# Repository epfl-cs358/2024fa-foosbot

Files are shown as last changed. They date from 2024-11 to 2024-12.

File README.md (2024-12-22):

# Foosbot

### Authors
- [Arthur Taieb](https://github.com/ArthurTota)
- [Ella Neike](https://github.com/Ella1807)
- [Tizian Kurz](https://github.com/TizianKurz)
- [Robin Nicole](https://github.com/Crowerade)
- [Nur Ertug](https://github.com/NurErtugn)

<details>
  <summary>Table of Contents</summary>
  <ol>
    <li>
      <a href="#project-overview">Project Overview</a>
      <ul>
        <li><a href="#built-with">Built With</a></li>
        <li><a href="#motivation">Motivation</a></li>
        <li><a href="#project-structure">Project Structure</a></li>
        <li><a href="#final-result">Final Result</a></li>
      </ul>
    </li>
    <li>
      <a href="#before-starting">Before Starting</a>
      <ul>
        <li><a href="#list-of-materials">List Of Materials</a></li>
        <li><a href="#requirements">Requirements</a></li>
      </ul>
    </li>
    <li>
      <a href="#doing-it-yourself">Doing It Yourself</a>
      <ul>
        <li><a href="#general-overview-of-tasks">General Overview Of Tasks</a></li>
        <li><a href="#lasercutting">LaserCutting</a></li>
        <li><a href="#3d-printing">3D Printing</a></li>
        <li><a href="#assembling-the-table">Assembling The Table</a></li>
      </ul>
    </li>
    <li>
      <a href="#wiring-of-the-motors">Wiring Of The Motors</a>
      <ul>
        <li><a href="#electronics-chart">Electronics Chart</a></li>
        <li><a href="#motor-and-endstop-sensor-labelling">Motor And EndStop Sensor Labelling</a></li>
        <li><a href="#protecting-motors-and-laptop">Protecting Motors And Laptop</a></li>
      </ul>
    </li>
    <li>
      <a href="#uploading-arduino-code">Uploading Arduino Code</a>
      <ul>
        <li><a href="#dependencies">Dependencies</a></li>
        <li><a href="#uploading-code">Uploading Code</a></li>
        <li><a href="#troubleshooting-arduino">Troubleshooting Arduino</a></li>
      </ul>
    </li>
    <li>
      <a href="#camera-vision">Camera Vision</a>
      <ul>
        <li><a href="#qr-code-markers">QR Code Markers</a></li>
        <li><a href="#code">Code</a></li>
        <li><a href="#installing-dependencies">Installing dependencies </a></li>
        <li><a href="#starting-camera-vision">Starting Camera Vision</a></li>
        <li><a href="#output">Output</a></li>
        <li><a href="#troubleshooting-camera-vision">Troubleshooting Camera Vision</a></li>
      </ul>
    </li>
  </ol>
</details>

## Project Overview

### Built With
* [][Python-url]
* [][Cpp-url]

### Motivation 
Table football, commonly known as foosball or table soccer, is a fast-paced game inspired by association football. Players aim to score goals by maneuvering rods with miniature figures representing football players from two opposing teams. While typically enjoyed by 2-4 players, traditional foosball is not designed for solo play.

This project seeks to develop a foosball table playable by a single player using an Arduino Uno microcontroller. The system will allow one side of the game to be automated and controlled via a computer program, while a human player operates the other side. The automated system will manage two axes of movement for each rod: rotation and linear displacement.

However, to simplify development and reduce costs, the prototype will use a smaller-scale foosball table with two rods per side instead of the standard four. This scaled-down design reduces system complexity and enhances motor responsiveness, making it more suitable for our project goals.

### Project Structure
- `Admin` : Contains images used in the README
- `CAD` : Contains all the CAD stl files as well as the dxf files for lasercutting
- `Hardware` : Contains the electronic circuit diagram and a document with hardware component specifications
- `Software` : Contains all the code
  - `Software/Algorithms/followBall` : Contains the Arduino code for controlling the motors and handling the game logic
  - `Software/Camera/cv/python-webcam` : Contains the python code for the computer vision as well as the QR Markers to printout

### Final Result 

https://github.com/user-attachments/assets/f8ba40bc-5658-4df2-8fb3-47cc1d8da43e

Table

Circuitry

<p align="right">(<a href="#readme-top">back to top</a>)</p>

## Before Starting

### List of Materials 
You will need to buy:
- [x] 4 17HS4401 Stepper Motors
- [x] 4 A4988 Motor Drivers
- [x] 4 End stop Sensors
- [x] 1 Arduino Uno
- [x] 1 USB cable to connect to the Arduino
- [x] 1 CNC Shield
- [x] 1 USB Isolator
- [x] 1 Logitech Webcam C270
- [x] 2 Aluminium Profile _20_ _x_ _20mm_ of length _410mm_
- [x] 1 12V Power Supply
- [x] 1 Power Supply Plug
- [x] 2 _~1_ _meter_ GT2 _6mm_ belt
- [x] 1 _1_ _meter_ WS2813 LED Strips
- [x] 1 Bread board
- [x] 2 Metal Bars with diameter _15_ _mm_ length _1200__mm_
- [x] 2 Metal Bars with diameter _8_ _mm_ length _1200__mm_
- [x] 4 Ball Bearings that allow for both rotational and linear motion
- [x] 8 Wheels (Something like [this](https://www.zyltech.com/zyltech-20-series-wheel-pulley-bearing-for-2020-aluminum-extrusion-v-slot-compatible/))
- [x] 2 Pully
- [x] Jumper cables
- [x] 1 ball

To assemble you also need the following

Pole Components:
- [x] 48 _M3_ screws with nuts, length _8mm_
- [x] 12 _M2.5_ screws with nuts, length _12mm_
- [x] 2 _M4_ screws with nuts, length _16mm_

Mechanical Components:
- [x] 14 _M3_ screws with nuts, length _8mm_
- [x] 2 _M3_ screws with nuts, length _25_mm
- [x] 16 x _M2.5_ screws with nuts, length _8mm_
- [x] 2 x steel bars, diameter _4mm_, length _3.2mm_
- [x] 2 x steel bars, diameter _4mm_, length _2.2mm_

### Requirements 
have access to:
  -	3D printer with TPU filament
  -	3D printer with PET filament
  -	Laser cutting machine
  -	PlexiGlass _10mm_
  -	MDF board _3mm_
  -	MDF board _4mm_
  -	MDF board _5mm_
  -	MDF board _10mm_
  -	Driller
  -	Bunch of different screwdrivers
  -	Soldering kit

<p align="right">(<a href="#readme-top">back to top</a>)</p>

## Doing it yourself

### General Overview of tasks
- Lasercut
- 3D Print
- Assemble the Table
- Wire up the motors to the Arduino
- Set up the Camera Vision

### LaserCutting
Lasercut with the right MDF thickness (is in the file names): [DXF files](CAD/laser_Cuted_Components) 

### 3D Printing
3D Print the following pieces from the CAD:

For 3D printing of Pole Components: [STL files](CAD/PoleComponents) 

- 4 x Players with _15mm_ radius (Computer Controlled) -> Perimeter 6
- 4 x Players with _8mm_ radius (Human Controlled)     -> Perimeter 6
- 2 x GardianStop _15mm_ radius                        -> Perimeter 2
- 2 x GardianStop _8mm_ radius                         -> Perimeter 2
- 4 x Bumpers with _15mm_ radius                       -> Perimeter 2
- 4 x Bumpers with _8mm_ radius                        -> Perimeter 2
- 8 x Bushing with _15mm_ radius                       -> Perimeter 3
- 8 x Bushing with _8mm_ radius                        -> Perimeter 3
- 2 x Handles                                          -> Perimeter 5
- 2 x End Caps _8mm_ radius                            -> Perimeter 3
- 2 x End Caps _15mm_ radius                           -> Perimeter 3

For 3D printing of Mechanical Components: [STL files](CAD/MechanicalComponents)
  
- 2 x Standing Motor holder                            -> Perimeter 2
- 2 x Rotation Motor holder                            -> Perimeter 2
- 2 x Motor to Pole Connector                          -> Perimeter 5
- 2 x Railing holder without pulley                    -> Perimeter 2
- 2 x Railing holder with pulley                       -> Perimeter 2
- 2 x pulley                                           -> Perimeter 2
- 2 x wheels (to put at the end of the belts)          -> Perimeter 2
- 4 x Belt to motor Platform Connector                 -> Perimeter 5

Our 3D printing steps: 
Use Fusion 360 to create and edit the pieces 

Open Prusaslicer to prepare pieces for impression: 
1. Select Filament PETG
2. Select Printer MK4 with 0.4 nozzle or i3 MK3S & MK3S+
3. Select Print Setting 0.20mm QUALITY
4. Place and add necessary supports to print out pieces correctly
5. Edit the perimeter of the pieces for more resistance if needed
6. Slice and Print

For the Bumpers:
Open Prusaslicer to prepare pieces for impression: 
1. Select Filament NinjaTek NinjaFlex TPU
2. Select Printer i3 MK3S & MK3S+
3. Select Print Setting 0.20mm QUALITY
4. ! don't use supports
5. Place pieces and Slice 
6. Add glue to printing bed
7. Print 

When slicing be careful of the surface on which you print your pieces, to ideally minimize supports needed or place them in a smart way. 

### Assembling The Table 
1. Glue all the mdf pieces together with wood glue
2. Add ball bearings and screw bushings
3. Insert poles in one bushing and add the bumpers, add players with a spacing of _184mm_ between player/gardianStop, add gardianStop
4. Insert poles into second bushing and add endcaps and handles
5. Follow picture in Final Result to finish assembly

Foosbot Assembly Animation

<p align="right">(<a href="#final_result_top">back to Final Result</a>)</p>

For ball reception place the following way
BallReception

<p align="right">(<a href="#readme-top">back to top</a>)</p>

## Wiring of the Motors

### Electronics Chart
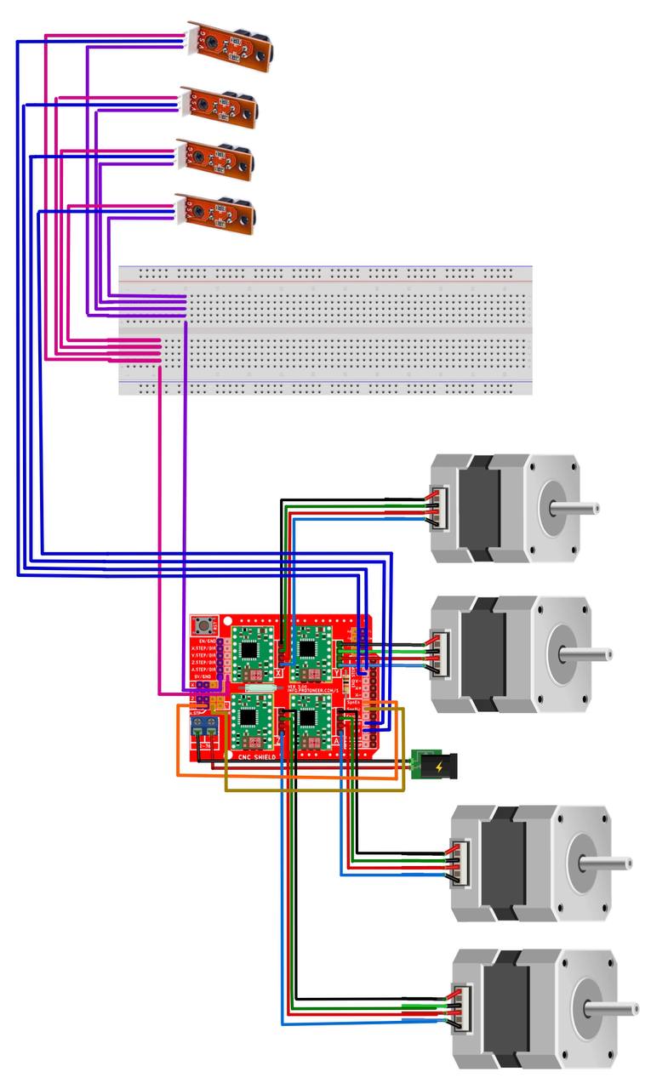
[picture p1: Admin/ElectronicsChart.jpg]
ElectronicCircuit


CNC shield mounted on top of the Arduino Uno , reset buttons should be aligned 
CNC shield-Arduino Uno pin correspondance
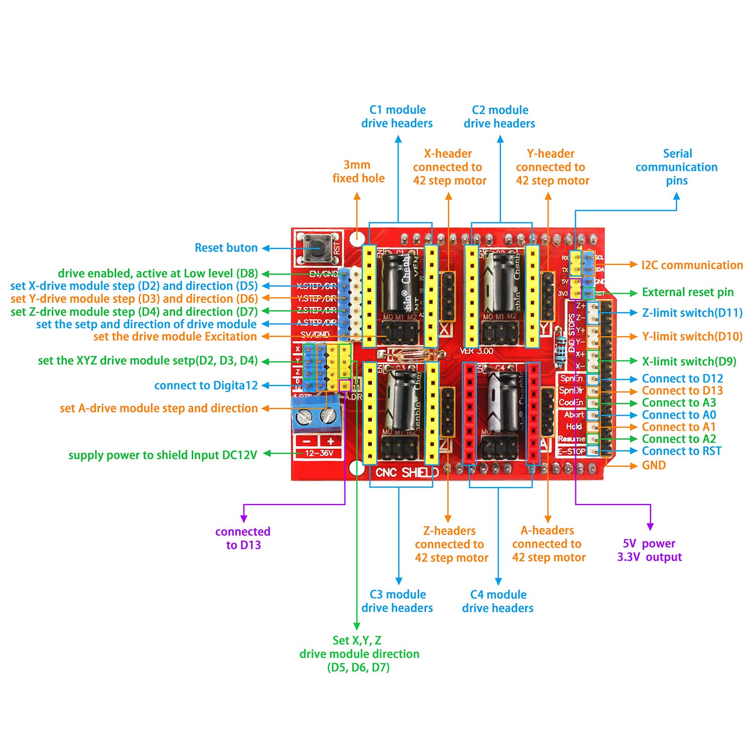
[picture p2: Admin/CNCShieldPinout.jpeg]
CNCShieldPinout


When installing the A4988 Motor Drivers set the voltage in alternate current to 1.2V
by turning the screws and using a multimeter. 

### Motor And EndStop Sensor Labelling
On the CNC Shield there are 3 slots for motor drivers labelled X, Y, Z, A. In the picture below you see to which motor they should be connected to.

The End stop sensors have three cables that need to be connected, one to the ground, one to the 5V Power and one to the correct pins on the CNC Shield. The mapping of the position of the end stop sensors to the pins on the CNC Shield are shown in green in the picture below.


### Protecting Motors and Laptop
Always connect the Arduino via a USB-Isolator to your laptop and ideally don't charge your laptop while it is connected to the Arduino.
It is also important that you unplug the power and the Arduino before changing anything on the wiring or manually moving the motors.
Generally it is also advised to disconnect the power and the arduino whenever you're not using them.
Also note that the motor drivers on the CNC shield might head up a bit if used for a long period of time.

<p align="right">(<a href="#readme-top">back to top</a>)</p>

## Uploading Arduino Code

### Dependencies
You need to have [Arduino IDE](https://www.arduino.cc/en/software) installed, as well as the libraries

### Uploading Code
1. Open the code for the Arduino in `/Software/Algorithms/followBall/followBall.ino`
2. Connect the Arduino via the USB Isolator to your laptop
3. Press the upload button in the top left of the Arduino IDE

### Troubleshooting Arduino

- If you get a compilation error, check whether you have all libraries installed.
- If you get an error while uploading, check whether you have selected the right board and port and try again.
- If the motors don't move check your wiring. If that doesn't help check the voltage of the motor drivers using a multimeter. Also the [documentation](https://docs.cirkitdesigner.com/component/2c4686b3-94a4-4df1-aee0-7a9f67fd5f2e/cnc-shield-v3) of the CNC shield might help.

<p align="right">(<a href="#readme-top">back to top</a>)</p>

## Camera Vision

### QR Code Markers
You need to print out the 4 QR Code Markers stored in the file
[`/Software/Camera/cv/python-webcam/ArUco markers.pdf`](https://github.com/epfl-cs358/2024fa-foosbot/blob/main/Software/Camera/cv/python-webcam/ArUco%20markers.pdf)
and cut them out. 

You then have to tape the QR Codes into the Right corners. Note that the top left corner, marked red in images below, should always point towards the corner. The QR Codes are numbered (see below) and they need to be in the right corners, according to the image below.

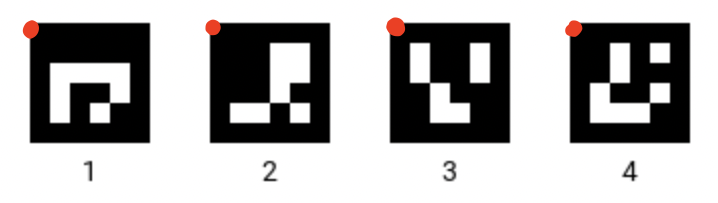
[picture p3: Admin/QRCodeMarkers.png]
QRCodeMarkers


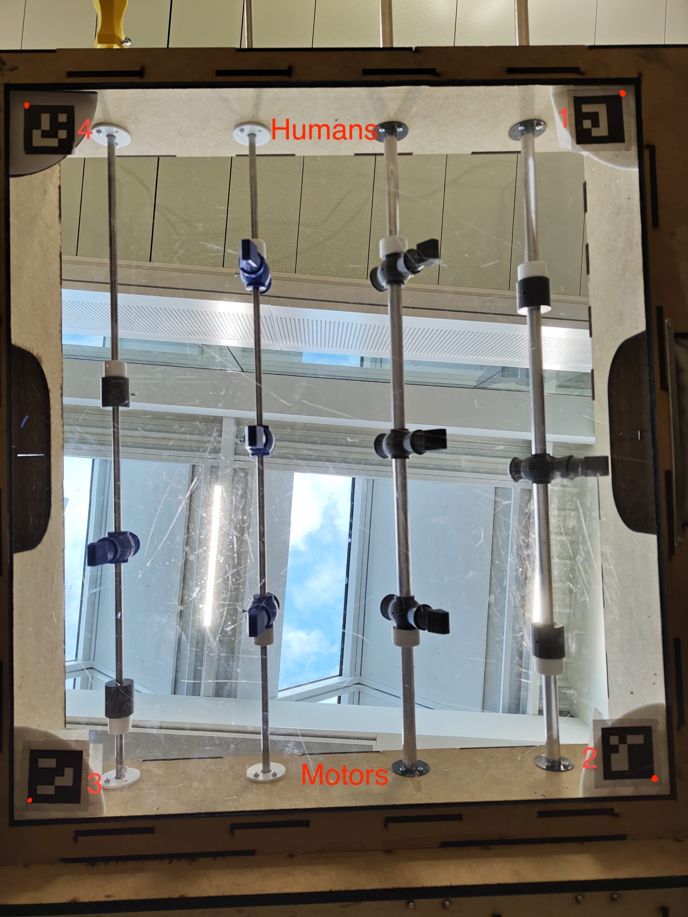
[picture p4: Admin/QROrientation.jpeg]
QROrientation


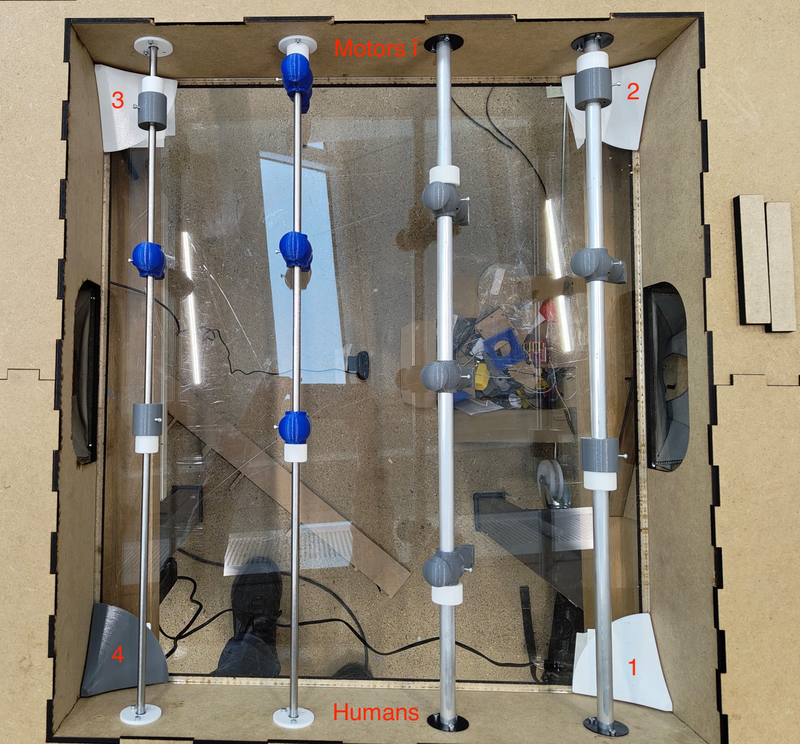
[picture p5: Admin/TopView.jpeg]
TopView


__It is important that the Codes are at in the right corners and oriented the right way!__
Otherwise the camera vision will not detect the playing field correctly and do a weird transformation or cut of some part.

### Code
The code for the Camera Vision is located in the folder
[`/Software/Camera/cv/python-webcam/main.py`](https://github.com/epfl-cs358/2024fa-foosbot/blob/main/Software/Camera/cv/python-webcam/main.py)

### Installing Dependencies
You need to have python installed on your computer (See [here](https://realpython.com/installing-python/) an article how to install python).
You als need the following libraries:
- [PySerial](https://pypi.org/project/pyserial/)
- [opencv](https://opencv.org/)

If you are on linux or macOS and have pip installed you can simply run 

```commandline
pip install pyserial
pip install opencv
```
If you're having trouble, check with your package manager whether it accepts pip installs.

### Starting Camera Vision
Note that you have to close all Serial monitors in the ArduinoIDE since it prevents the computer vision from opening the port. You can open it again when the computer vision is running.
2. Plug in the Logitech webcam,
1. Plug in the Arduino UNO,
3. Navigate to folder ` Software/Camera/cv/python-webcam `,
4. Run ` ./main.py `.

If you want to know how to use different flags, type `./main.py --help`.

### Output

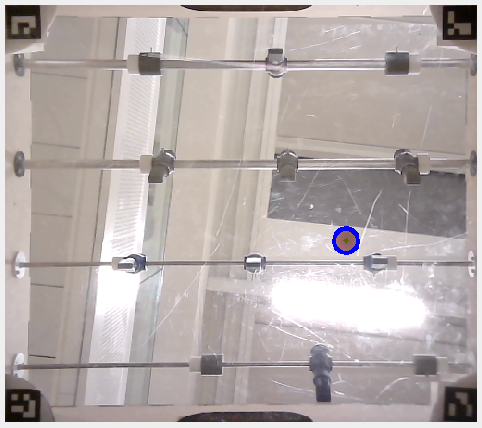
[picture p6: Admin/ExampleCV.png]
ExampleCV


By default the camera should open a window called Output which displays the area in which the ball can be detected. If  the ball is detected, there should be a blue circle around it.

### Troubleshooting Camera Vision
- If the camera is not activating properly, try changing the parameter of the call to the ` cv2.VideoCapture ` function to another number (usually 0 or 2). You can also use the `-i` flag for that.
- If the camera vision does a weird transformation then the QR Codes are not placed in the right corners.
- If the output doesn't show the entire field, then the QR Codes might not be oriented correctly (Top left corner ins't pointing towards the corner).
- If the ball isn't detected then you might need to change the allowed range for the radius (line 37 in [`main.py`](https://github.com/epfl-cs358/2024fa-foosbot/blob/main/Software/Camera/cv/python-webcam/main.py)). By default it is set to accept radius between 25 and 31. This works well for us on Macbooks but we observed that on Linux a range of 10 to 15 is appropriate.
- If the code has a problem uploading to the arduino try doing the following (sometimes the port has a problem):
1. Stop the computer vision
2. Make sure you have no serial monitor open on the arduino ide and close all other sketches
3. Plug in the arduino uno again and upload the code
4. Start the computer vision again 

Remember that you can use different flags to debug the computer vision. For example you can display views of different stages of computer vision (Marker detection, image transformation, etc.) using the --w or --windows flag or you can disable the Serial output if no Arduino is connected by  using the -n or --no-ser-out flag.

<p align="right">(<a href="#readme-top">back to top</a>)</p>

[Python.org]: https://img.shields.io/badge/Python-brightgreeen?style=flat&logo=python&logoColor=FFE873&color=306998
[Python-url]: https://www.python.org/
[Cpp.org]: https://img.shields.io/badge/C%2B%2B-blue?logo=cplusplus
[Cpp-url]: https://isocpp.org/

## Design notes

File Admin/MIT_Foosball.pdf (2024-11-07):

# Foosbot: A Single Player Table Football

CS-358: Making Intelligent Things — Team Project Proposal

Group Members:
Nur Ertug, Tizian Kurz, Arthur Taieb, Robin Nicole, Ella Neike

## Description

Table football, also known as foosball or table soccer, is a game based on association football. The objective is to move the ball into the opponent’s goal by manipulating rods with figures resembling football players of two opposing teams. This fast-paced game is typically played by 2-4 players, but it is not designed for solo play.
Our project proposes the creation of a Foosball table that can be played by a single player, with the help of an Arduino Uno board. Our vision involves a program executed from a computer connected to the microcontroller, controlling one side of the game, while a human player controls the other side. This system should at least be able to rotate the handles and displace them, considering two axes of movement per pole.
A traditional foosball table is as large as a standard table and has four handles per side. However, for the sake of our project’s budget and complexity, the prototype will be based on a smaller version with only two handles per side. This approach will reduce system complexity and improve motor reaction times.

## Game Setup

- A red button is placed on one side of the main game surface to activate the game.
- The button can be pressed during the game to stop the action and restart the game.
- Double-clicking the red button stops the game completely.
- A small digital screen shows:

– Game Instructions

– Current score while playing

1

## Game Level Selection

The single player can choose their competitor’s difficulty level: beginner, intermediate, or advanced.

## Player Specification

The player can select their team color and name via the digital screen. When the player scores, a special congratulatory message will be displayed on the screen.

## Gameplay Mechanics

Controls

The human player uses keyboard controls or mouse inputs to control the players. Instructions will be provided on how to maneuver.

Game Rules

Standard foosball rules apply.

Game Levels

- Beginner: Basic movements with error replacement in shooting skills.
- Intermediate: Better positioning, including ball passing between players on the same row.
- Advanced: Fast moves, improved tactics based on the human player’s actions.

## Visuals and Sound

- Sound: Hand clap sound effects when the single player scores.
- Visuals: Congratulatory messages displayed on the digital screen when the player scores.

## Game Flow Parametrics

- Digital Display: Displays current score.
- Red Button: Controls for resetting, starting, and stopping the game.
- Match Timer: A 30-minute counter automatically ends the game.

2

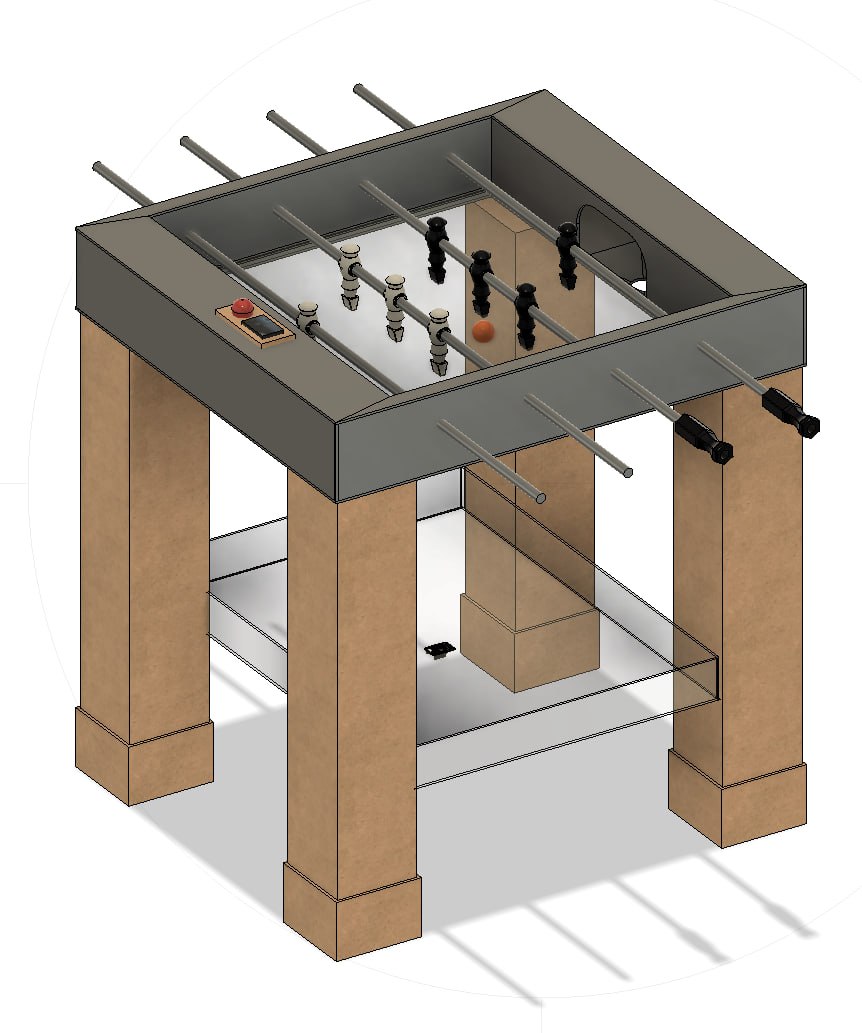
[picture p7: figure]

Figure 1: Isometric View of Foosball Table Structure

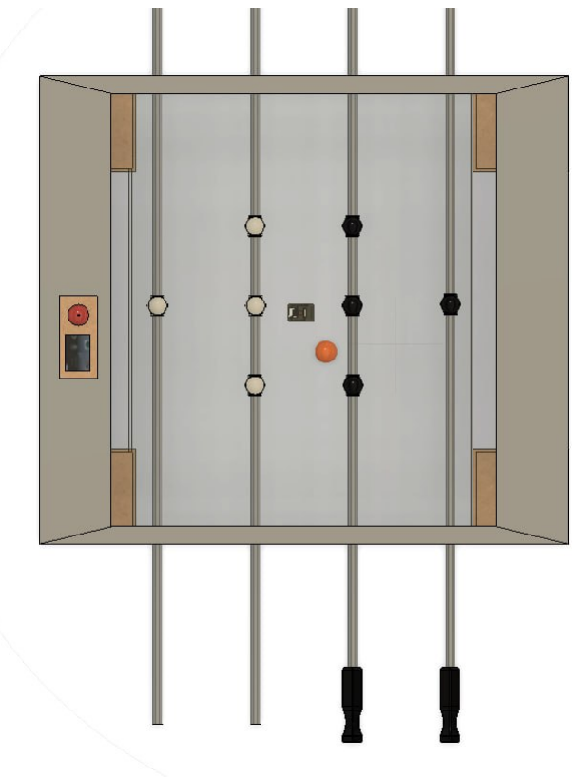
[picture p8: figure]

Figure 2: Top View of the Foosball Table Structure

3

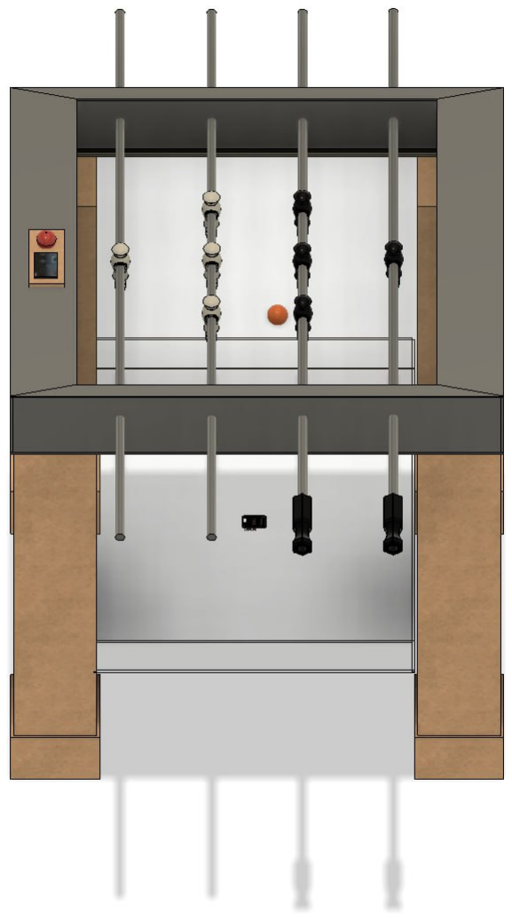
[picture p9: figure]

Figure 3: Side Elevation View of Foosball Table with Players

4

## Technical and Mechanical Details

Ball Vision

A camera is installed underneath the foosball setting, with a transparent surface of the game. The chosen camera model is ESP32-CAM. Due to possible challenges that top-view angle can introduce such as blind spots of the ball positions, we chose a transparent ground system for camera vision.
The ball has a distinct color such as violet for the camera vision to be able to separate it from the object in the camera view.

Image Processing And Motor Control

To accurately detect the players’ positions and control their movements during the game, we will use a combination of sensors managed by Arduinos. There will be two key sensors: one attached to the rotation motion motor and an end-stop sensor for the sideways motion of the bar.
The sensor on the rotation motor will track each player’s angular position, allowing precise control of their turning movements. Meanwhile, the end-stop sensor will manage the sideways motion of the bar, ensuring that it always starts from a consistent position at the beginning of each game.
The Arduinos will be programmed to interpret data from both sensors, enabling precise adjustments to the players’ rotation and sideways motion. This setup will ensure accurate player positioning and smooth movements, providing a consistent and reliable gameplay experience.

Motor Design

The motors controlling the AI-player rods are responsible for two key functionalities: linear motion and rotational motion.
Linear motion refers to the movement of the rod along the x-axis on the playing field, primarily used for blocking incoming shots or passing the ball to one of the AI players on the same row. The precision and accuracy of this movement are achieved using stepper motors, which are driven by A4988 motor drivers. These motor drivers not only provide fine control over the rod’s positioning but also supply the necessary power for the actuation, since the motors cannot be powered directly from the controller.
Rotational motion can be described as the actuation of the angular coordinate in a polar system with a fixed radius, where the rod rotates about a point offset along the x-axis rather than moving along the y-axis. This motion allows the AI players to perform actions such as kicking or blocking, reacting to the ball’s direction by rotating quickly. The Racestar 3536 motors are employed for this task, delivering high torque to enable fast and powerful rotational movement. These motors are also controlled by suitable motor drivers to ensure they receive adequate power for their operation.
For sensor feedback:

5

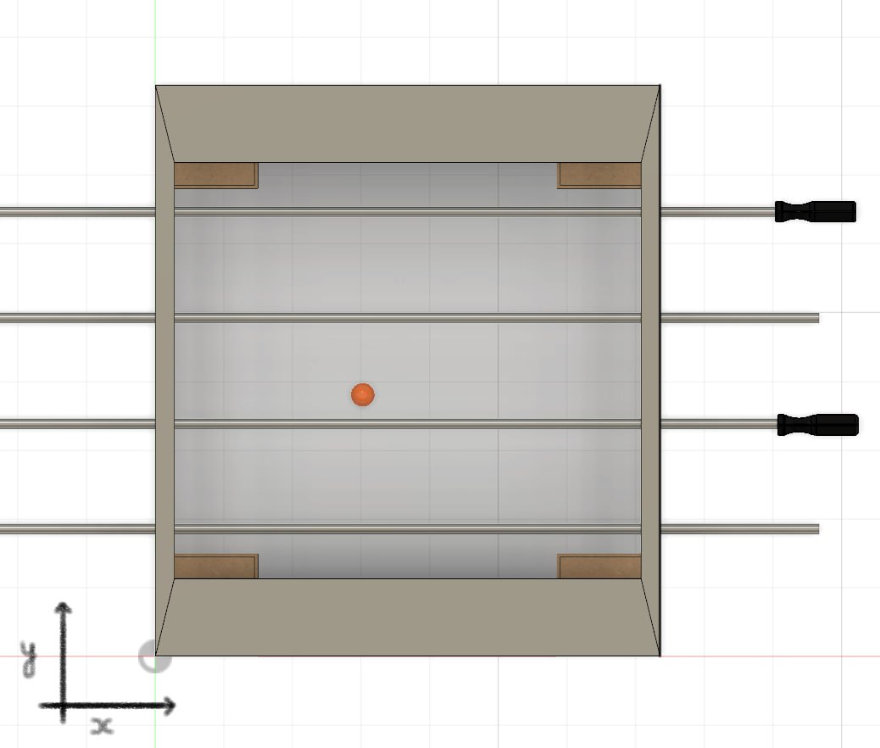
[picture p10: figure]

Figure 4: Top View with the Description of the Axis Structure

Rotary Incremental Encoders are attached to each motor to provide precise data on the angular position of the rods, ensuring that rotational movements are responsive and accurate in real time. End Stop sensors detect the maximum and minimum travel positions of the rods during linear motion, ensuring smooth operation and preventing the rods from moving out of bounds.
Regarding the mechanical design that allows the rods to move sideways and rotate, there are two components. The first one allows the rods to move sideways, and the second on allows them to rotate. As a model, the CAD files exhibit the intended mechanism:
- To move sideways: the idea is to use a cylinder that wraps around the rod without any friction on it and can push or pull against rings that are stuck to the rods
- To rotate: the original idea was to wrap a long gear around the rod and rotate it, however as it would imply technical difficulties another idea would be to use only two small gears far apart and connect them with small rods to allow the gear to rotate. Again, another idea would be to attach the motor to the end of the rod.

## Risk Assessment

- User Experience Risk: The AI player’s movements at different levels may seem robotic and unrealistic.
- Technical Risk: The response time of AI players may not be quick enough.
- Electronics and Wiring Risk: Risks include short circuits, unique ground levels, and motor-related risks such as back EMF, magnetic interference, and blunt trauma, as described in the course manual.

6

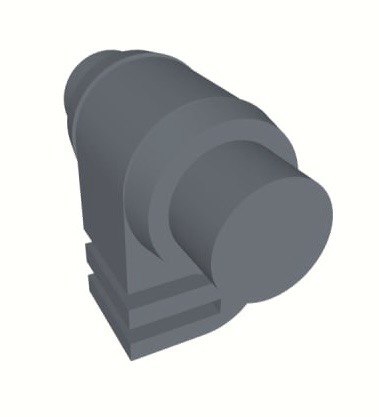
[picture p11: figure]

Figure 5: Side Part Design

- Lighting Conditions: The performance of color-based tracking can be sensitive to changes in lighting conditions, which could cause the color detection to fail. Calibration of thresholds may be necessary if lighting changes significantly.
- Occlusion: If the ball or player feet overlap or occlude each other, it may be difficult for the camera to distinguish between them, especially if they have similar colors.

Previous Projects

Automated Baby-Foot Table - Instructables (https://www.instructables.com/Automated-Baby-Foot-Table-Simplified/)

Babyfoot Upgrade Report - EPFL (https://www.epfl.ch/labs/la/wp-content/uploads/2018/08/LeoSibut2016_Babyfoot_upgrade_rapport-1.pdf)

Babyfoot 2020 Report - EPFL (https://www.epfl.ch/labs/la/wp-content/uploads/2020/12/Rapport-Babyfoot-2020-Projet-dingenieurie-simulatanee-1.pdf)

Robopong 2024 Report - EPFL (https://github.com/epfl-cs358/2024sp-robopong)

## Bill of Materials

You can also find the Bill of materials here (https://docs.google.com/document/d/1LACxbsoiZFoJ4g7a7IhW2nk5J2euQTXyOZ44LrSxmBQ/edit) in google Docs. The total cost is 240.45 CHF.

7

Type | Name | Shop | Qte. | Price per Piece (CHF) | Total Price (CHF)
Motor + Driver | 17HS4401 + A4988 | CS-358 | 2 | 15 | 30
Motor | Racerstar 3536 | CS-358 | 2 | 15 | 30
Motor Driver | b-g431b-esc1 | CS-358 | 2 | 18 | 36
Sensors | End Stop Sensor | https://www.bastelgarage.ch/optischer-endschalter-lichtschranke-mit-kabel (https://www.bastelgarage.ch/optischer-endschalter-lichtschranke-mit-kabel) | 4 | 3.50 | 14
Motor Sensors | CUI AMT-102-V Rotary Incremental Encoder | CS-358 | 2 | 21 | 42
Camera | ESP32-CAM | CS-358 | 1 | 4 | 4
USB Isolator | USB Isolator | CS-358 | 1 | 15 | 15
Power Supply | 78 W, 12 V, 6,5 A Power supply | https://www.reichelt.com/ch/fr/bloc-d-alimentation-de-table-78-w-12-v-6-5-a-vt-3240-p215629.html (https://www.reichelt.com/ch/fr/bloc-d-alimentation-de-table-78-w-12-v-6-5-a-vt-3240-p215629.html) | 1 | 18.90 | 18.90
Plug | Power Supply Plug | https://www.distrelec.ch/fr/jack-de-puissance-prise-femelle-angle-droit-x6-3mm-cliff-fc681465/p/14205870 (https://www.distrelec.ch/fr/jack-de-puissance-prise-femelle-angle-droit-x6-3mm-cliff-fc681465/p/14205870) | 1 | 2.25 | 2.25
Converter | Step Down Con-verter | https://www.reichelt.com/ch/fr/cartes-de-d-veloppement-r-gulateur-de-tension-20-w-convertiss-debo-dcdc-20w-p233018.html (https://www.reichelt.com/ch/fr/cartes-de-d-veloppement-r-gulateur-de-tension-20-w-convertiss-debo-dcdc-20w-p233018.html) | 2 | 4.53 | 9.06
Belts | GT2 6mm belt, 1m | https://www.bastelgarage.ch/gt2-riemen-6mm (https://www.bastelgarage.ch/gt2-riemen-6mm) | 2 | 3.90 | 7.80
LEDs | LED Strip, WS2813, 1m, 5V, 1.8A, 9W | https://www.distrelec.ch/en/led-strip-ws2813-1m-5v-8a-9w-rgb-seeed-studio-104020108/p/30121593 (https://www.distrelec.ch/en/led-strip-ws2813-1m-5v-8a-9w-rgb-seeed-studio-104020108/p/30121593) | 1 | 6.70 | 6.70
Button | Red Button | https://www.reichelt.com/ch/fr/shop/produit/ bouton d arcade rouge-317435 (https://www.reichelt.com/ch/fr/shop/produit/bouton_d_arcade_rouge-317435) | 1 | 1.29 | 1.29
Screen | Small Screen | https://www.reichelt.com/ch/fr/shop/produit/ cartes de developpement -cran e-ink 2 7 noir blanc-224220 (https://www.reichelt.com/ch/fr/shop/produit/cartes_de_developpement_-_cran_e-ink_2_7_noir_blanc-224220) | 1 | 19.95 | 19.95
Ball | 8 Orange Ball | https://andysbillard.ch/FB-Tischfussball-Ball-hart-orange (https://andysbillard.ch/FB-Tischfussball-Ball-hart-orange) | 1 | 3.50 | 3.50

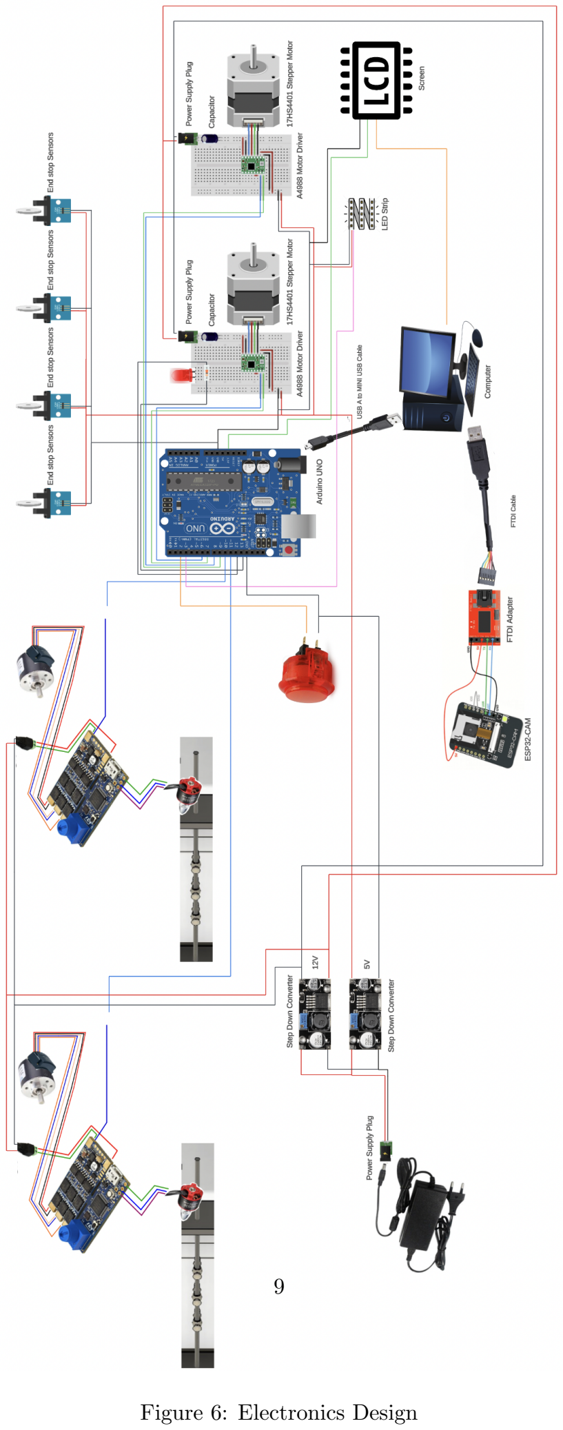
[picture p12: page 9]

Figure 6: Electronics Design

9

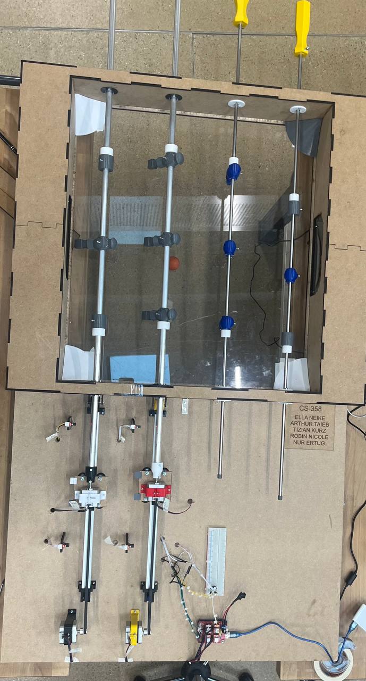
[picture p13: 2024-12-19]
Photo/TopView.jpg

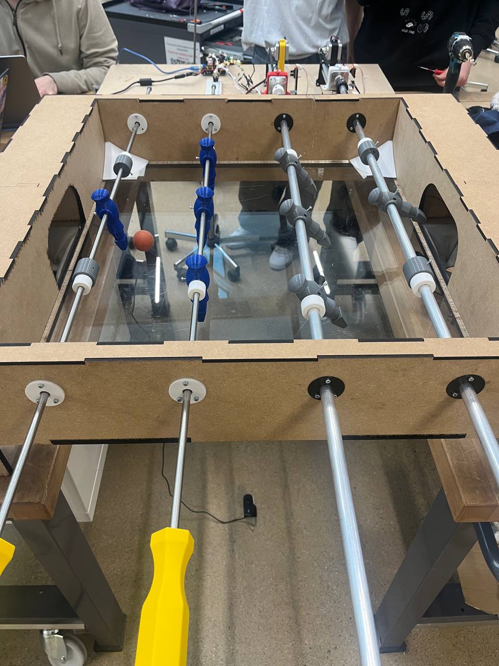
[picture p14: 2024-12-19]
Photo/Table.jpg

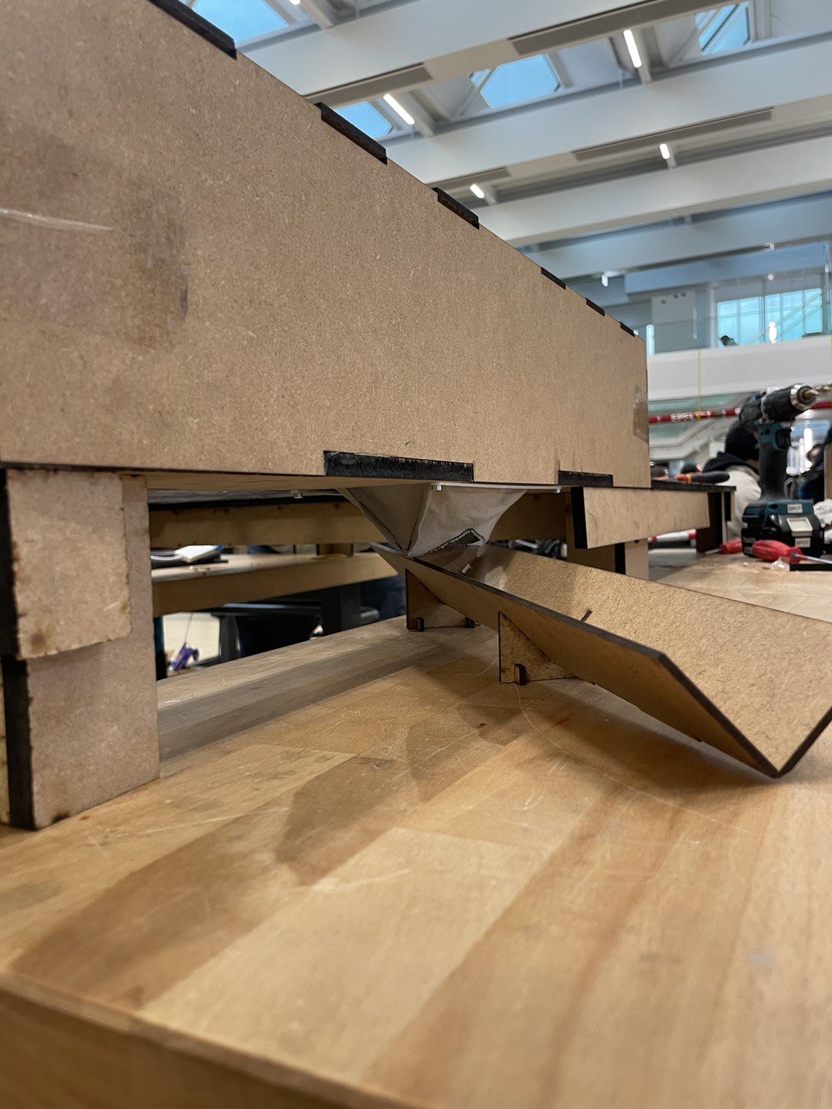
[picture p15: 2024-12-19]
Photo/BallReception.jpg

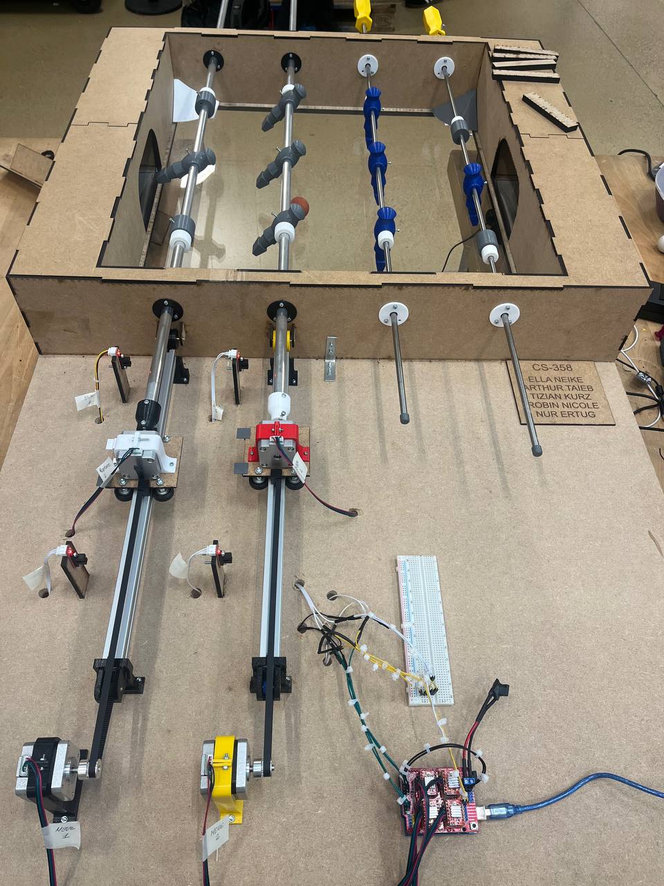
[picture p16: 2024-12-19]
Photo/Circuitry.jpg

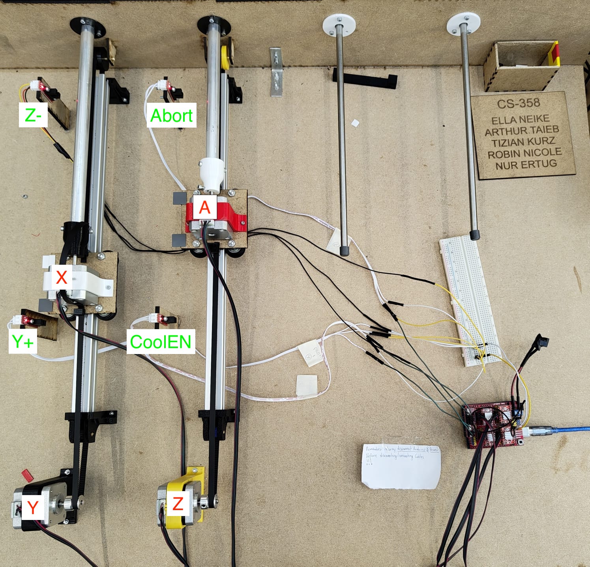
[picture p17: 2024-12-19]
Admin/MotorLabels.jpeg

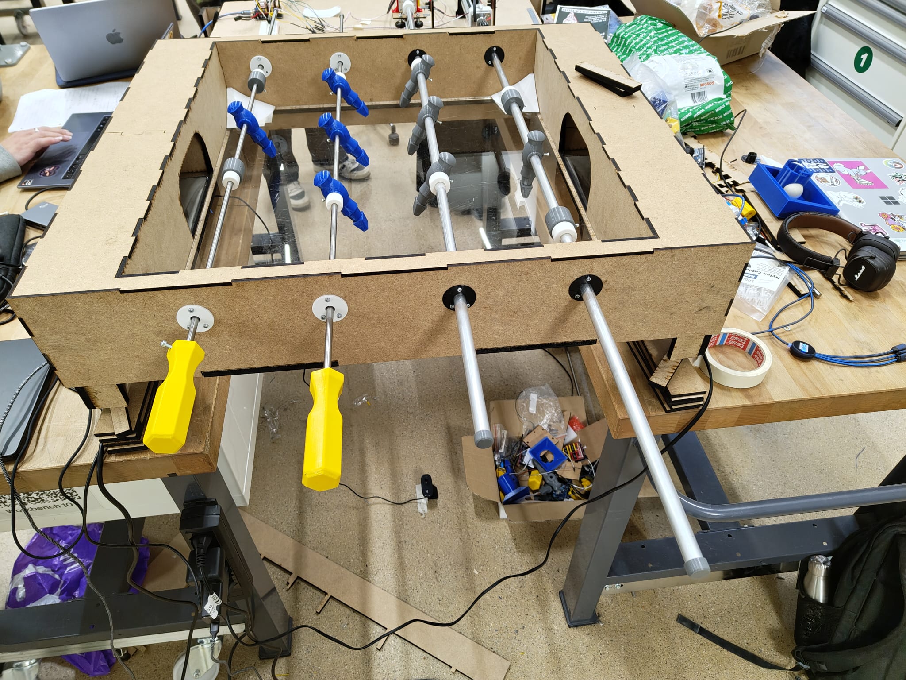
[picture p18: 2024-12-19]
Admin/table.jpeg

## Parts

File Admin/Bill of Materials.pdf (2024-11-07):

Bill Of Materials

Type | Name | Shop | Qte. | Price per piece (CHF) | total price (CHF)
Motor + Driver | 17HS4401 + A4988 | CS-358 | 2 | 15 | 30
Motor | Racerstar 3536 | CS-358 | 2 | 15 | 30
Motor Driver | b-g431b-esc1 | CS-358 | 2 | 18 | 36
Sensors | End Stop Sensor | https://www.bastelgarage.ch/optischer-endschalter-lichts chranke-mit-kabel (https://www.bastelgarage.ch/optischer-endschalter-lichtschranke-mit-kabel) | 4 | 3.50 | 14
Motor Sensors | CUI AMT-102-V Rotary Incremental Encoder (for FOC), indexes | CS-358 | 2 | 21 | 42
Camera | ESP32-CAM | CS-358 | 1 | 4 | 4
USB Isolator | USB Isolator | CS-358 | 1 | 15 | 15
Power Supply | 78 W, 12 V, 6,5 A Power supply | https://www.reichelt.com/ch/fr/bloc-d-alimentation-de-tabl e-78-w-12-v-6-5-a-vt-3240-p 215629.html (https://www.reichelt.com/ch/fr/bloc-d-alimentation-de-table-78-w-12-v-6-5-a-vt-3240-p215629.html) | 1 | 18.90 | 18.90
Plug | Power Supply Plug | https://www.distrelec.ch/fr/ja ck-de-puissance-prise-femel le-angle-droit-x6-3mm-cliff-f c681465/p/14205870 (https://www.distrelec.ch/fr/jack-de-puissance-prise-femelle-angle-droit-x6-3mm-cliff-fc681465/p/14205870) | 1 | 2.25 | 2.25
Converter | Step Down Converter | https://www.reichelt.com/ch/fr/cartes-de-d-veloppement-r -gulateur-de-tension-20-w-c onvertiss-debo-dcdc-20w-p2 33018.html (https://www.reichelt.com/ch/fr/cartes-de-d-veloppement-r-gulateur-de-tension-20-w-convertiss-debo-dcdc-20w-p233018.html) | 2 | 4.53 | 9.06
Belts | GT2 6mm belt, 1m | https://www.bastelgarage.ch/gt2-riemen-6mm (https://www.bastelgarage.ch/gt2-riemen-6mm) | 2 | 3.90 | 7.80
LEDs | LED Strip, WS2813, 1m, 5V, 1.8A, 9W | https://www.distrelec.ch/en/l ed-strip-ws2813-1m-5v-8a-9 w-rgb-seeed-studio-104020 108/p/30121593 (https://www.distrelec.ch/en/led-strip-ws2813-1m-5v-8a-9w-rgb-seeed-studio-104020108/p/30121593) | 1 | 6.70 | 6.70
Button | Red Button | https://www.reichelt.com/ch/fr/shop/produit/bouton_d_arc (https://www.reichelt.com/ch/fr/shop/produit/bouton_d_arcade_rouge-317435) | 1 | 1.29 | 1.29

Type | Name | Shop | Qte. | Price per piece (CHF) | total price (CHF)
| | ade_rouge-317435 (https://www.reichelt.com/ch/fr/shop/produit/bouton_d_arcade_rouge-317435)
Screen | Small Screen | https://www.reichelt.com/ch/fr/shop/produit/cartes_de_developpement_-_cran_e-ink_2_7_noir_blanc-224220 (https://www.reichelt.com/ch/fr/shop/produit/cartes_de_developpement_-_cran_e-ink_2_7_noir_blanc-224220) | 1 | 19.95 | 19.95
Ball | Orange Ball | https://andysbillard.ch/FB-Ti schfussball-Ball-hart-orange (https://andysbillard.ch/FB-Tischfussball-Ball-hart-orange) | 1 | 3.50 | 3.50

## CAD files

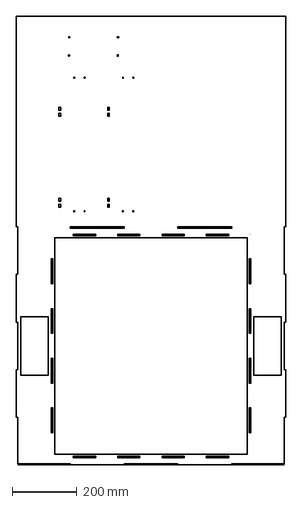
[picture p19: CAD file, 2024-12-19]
CAD/laser_Cuted_Components/ALLdxfTOcut/MDF/10mm/Bottom.dxf
830.0 x 1385.0 mm

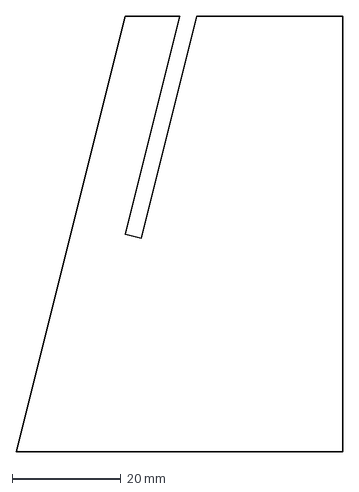
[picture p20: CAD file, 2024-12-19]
CAD/laser_Cuted_Components/ALLdxfTOcut/MDF/3mm/GoalBallStopper/socle.dxf
60.0 x 80.0 mm

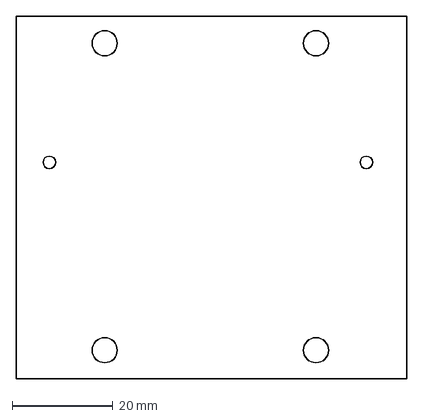
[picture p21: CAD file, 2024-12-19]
CAD/laser_Cuted_Components/ALLdxfTOcut/MDF/3mm/railBoardForMotor.dxf
77.5 x 72.0 mm

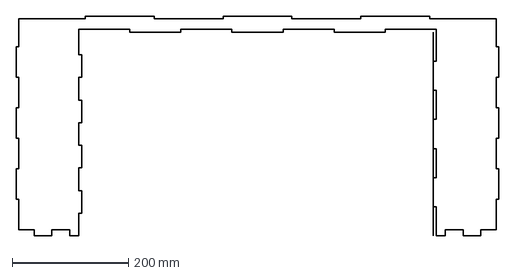
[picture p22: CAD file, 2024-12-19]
CAD/laser_Cuted_Components/ALLdxfTOcut/MDF/4mm/TopMotorSide.dxf
830.0 x 377.5 mm

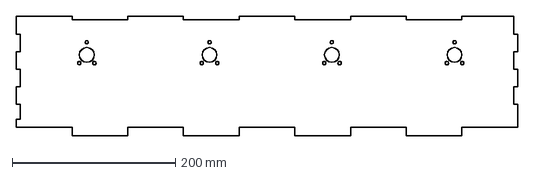
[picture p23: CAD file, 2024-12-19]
CAD/laser_Cuted_Components/ALLdxfTOcut/MDF/5mm/internPlayerSide.dxf
615.0 x 146.1 mm

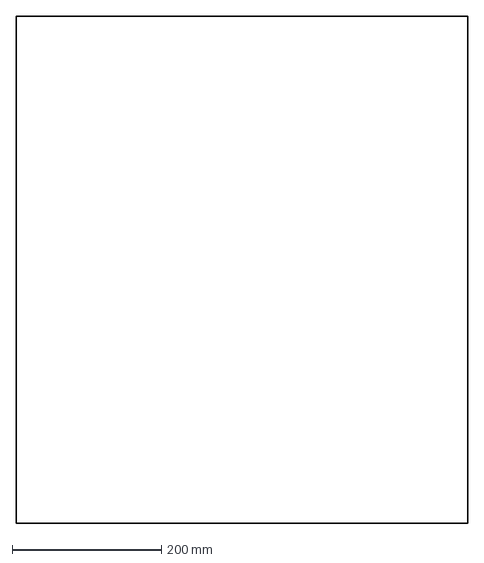
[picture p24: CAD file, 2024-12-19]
CAD/laser_Cuted_Components/ALLdxfTOcut/Plexiglass/GroundFiledTransparent.dxf
605.0 x 680.0 mm

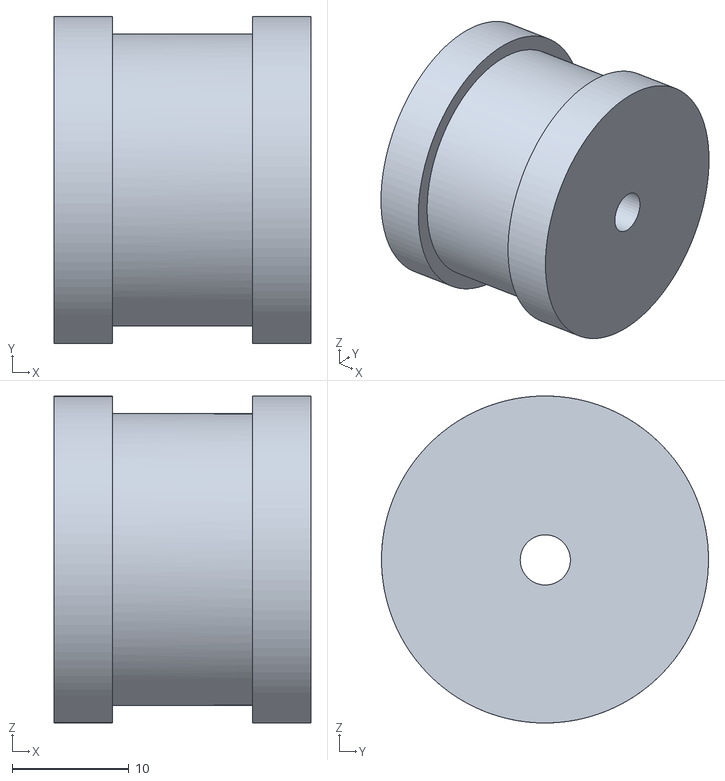
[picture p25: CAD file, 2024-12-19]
CAD/Mechanical_3d_printed/STL_Mechanic/BigPlasticPulley.stl
22.0 x 28.0 x 28.0

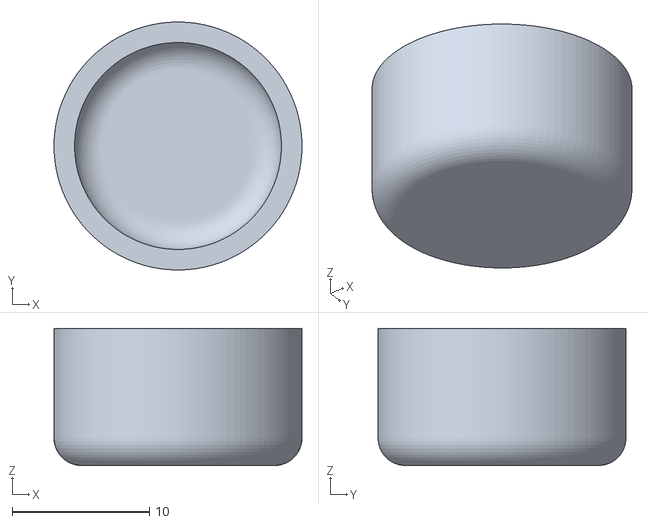
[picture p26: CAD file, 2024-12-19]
CAD/PoleComponents/end cap 8mm.stl
18.1 x 18.1 x 10.0

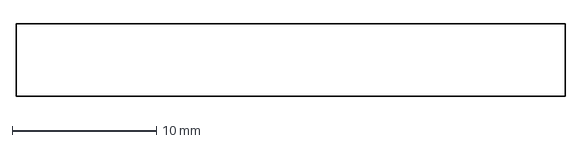
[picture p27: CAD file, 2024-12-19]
CAD/laser_Cuted_Components/ALLdxfTOcut/MDF/3mm/BlockerPulleyHolder.dxf
38.0 x 5.00 mm

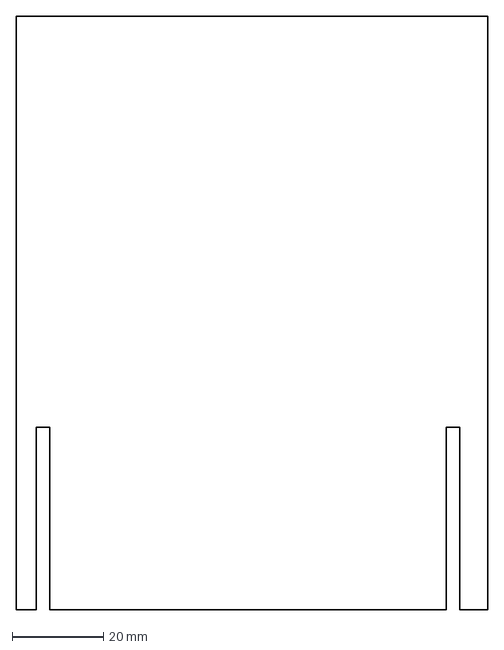
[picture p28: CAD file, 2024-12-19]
CAD/laser_Cuted_Components/ALLdxfTOcut/MDF/3mm/GoalBallStopper/Mur.dxf
103.4 x 130.0 mm

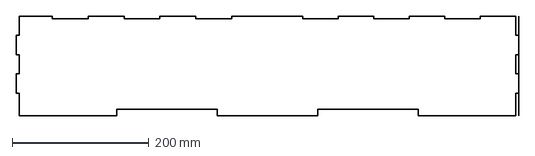
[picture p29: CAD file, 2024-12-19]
CAD/laser_Cuted_Components/ALLdxfTOcut/MDF/4mm/ExternGoallyPlayerSide.dxf
735.0 x 146.1 mm

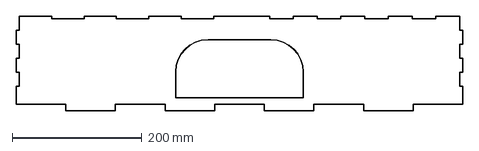
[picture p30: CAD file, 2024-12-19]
CAD/laser_Cuted_Components/ALLdxfTOcut/MDF/5mm/InternGoalMotorSide.dxf
690.0 x 146.1 mm

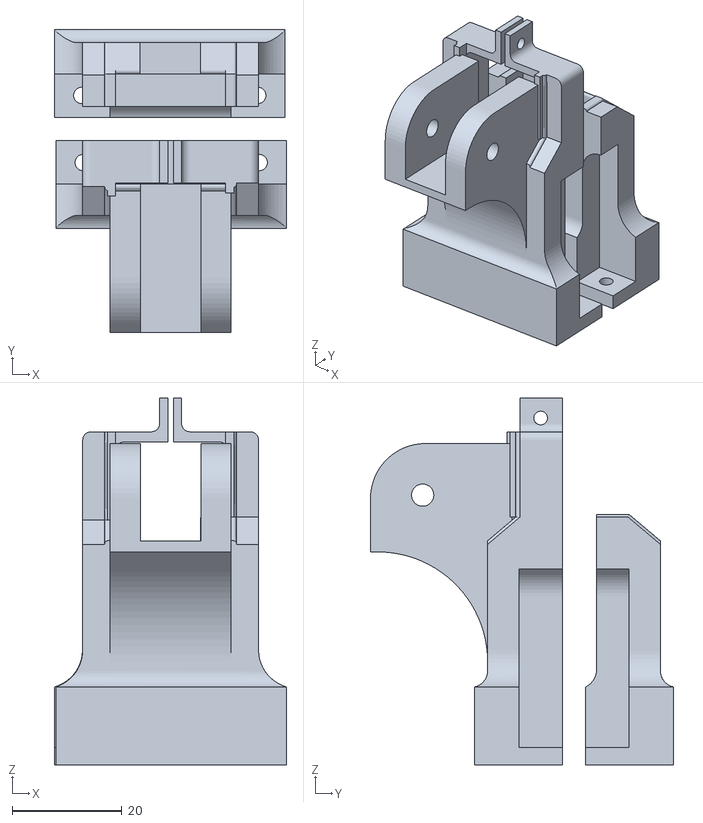
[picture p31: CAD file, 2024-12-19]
CAD/Mechanical_3d_printed/STL_Mechanic/AluminiumHolders.stl
42.3 x 55.1 x 66.8

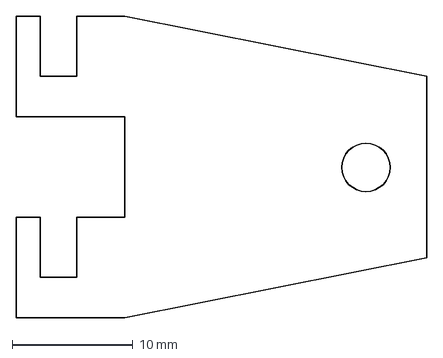
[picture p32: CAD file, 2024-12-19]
CAD/laser_Cuted_Components/ALLdxfTOcut/MDF/3mm/PulleyHolder.dxf
34.0 x 25.0 mm

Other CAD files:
CAD/laser_Cuted_Components/ALLdxfTOcut/MDF/4mm/TopPlayerSide.dxf
CAD/laser_Cuted_Components/ALLdxfTOcut/MDF/5mm/internMotorSide.dxf
CAD/Mechanical_3d_printed/STL_Mechanic/SidewayMotorHolder.stl
CAD/ElectronicComponents/17HS4401S Stepper Motor.f3d
CAD/ElectronicComponents/A4988-Stepper-Driver-WithPins.f3d
CAD/ElectronicComponents/ESP32-cam.f3d
CAD/ElectronicComponents/Optical endstop.f3d
CAD/ElectronicComponents/arduinouno.f3d
CAD/ElectronicComponents/small_breadboard.f3d
CAD/Mechanical_3d_printed/STL_Mechanic/AdptaterNemaToPole.stl
CAD/Mechanical_3d_printed/STL_Mechanic/PlasticGear.stl
CAD/Mechanical_3d_printed/STL_Mechanic/RotationMotorHolder.stl
CAD/Mechanical_3d_printed/STL_Mechanic/StrapHolder.stl
CAD/Mechanical_3d_printed/STL_Mechanic/endStopActivator_.stl
CAD/PoleComponents/Bumper Ninjaflex 15mm.stl
CAD/PoleComponents/Bumper Ninjaflex 8mm.stl
CAD/PoleComponents/bushing 15mm.stl
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

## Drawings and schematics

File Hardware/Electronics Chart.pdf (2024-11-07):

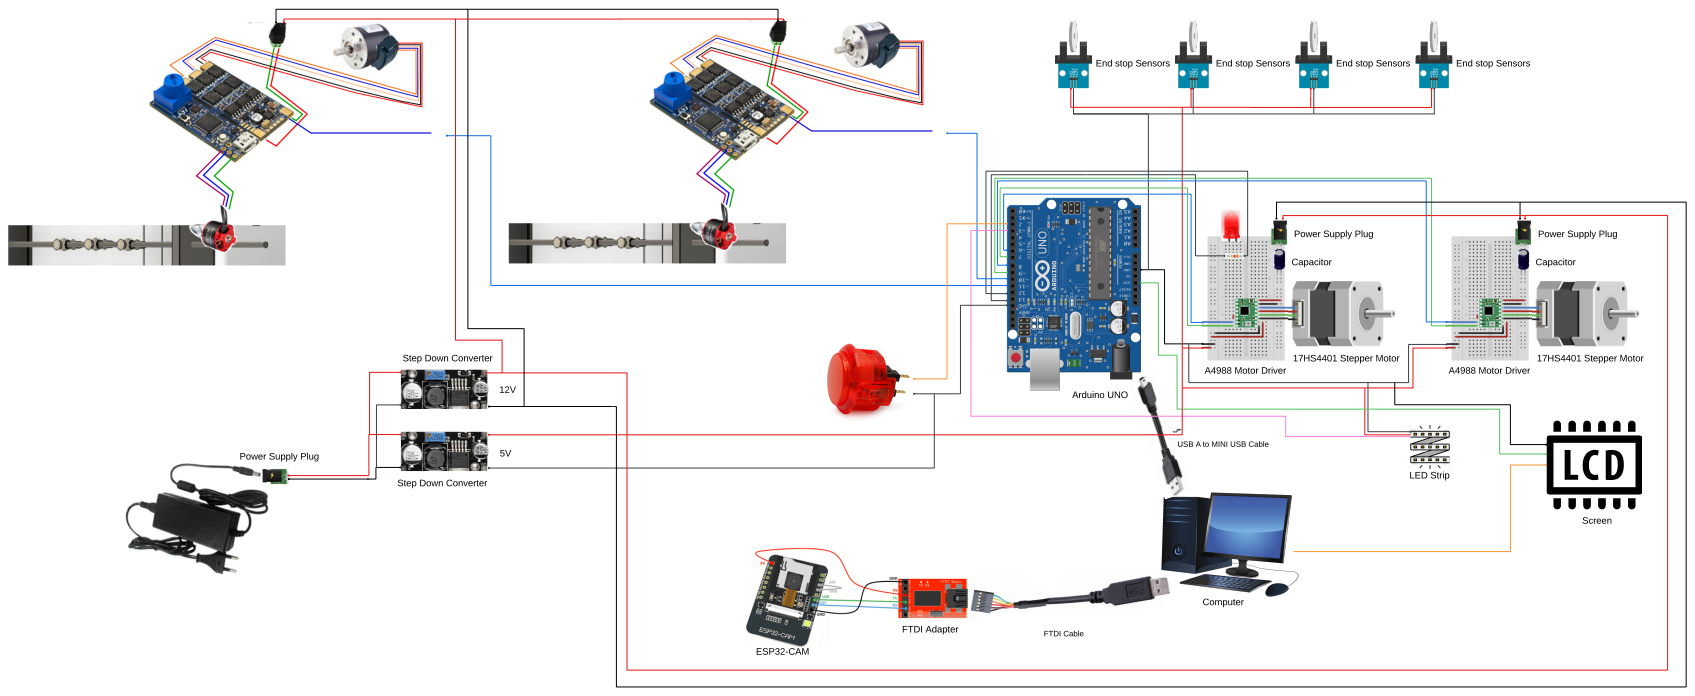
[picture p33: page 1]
ESP32-CAM; FTDI Adapter; Computer; Arduino UNO; 17HS4401 Stepper Motor; A4988 Motor Driver; Capacitor; FTDI Cable; End stop Sensors; LED Strip; Screen

End stop Sensors

Power Supply Plug

Step Down Converter

USB A to MINI USB Cable

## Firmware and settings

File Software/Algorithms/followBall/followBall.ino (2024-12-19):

#include <stdio.h>
#include <math.h>
#include "ParallelInterpreter.h"
//#include "ConstantsForMac.h"
#include "ConstantsForLinux.h"

/*************
 * Constants *
 *************/

// Dimensions //

#define FIELD_WIDTH   680
#define FIELD_HEIGHT  605

#define FIELD_SIZE 1300

// Scaling factors //

#define SCALE_X ((double)FIELD_WIDTH / CAM_WIDTH)
#define SCALE_Y ((double)FIELD_HEIGHT/ CAM_HEIGHT)

#define FIELD_X_TO_MU 5 // Converts from millimeters to motor units on the X
                        // axis

#define CV_TO_MM(VALUE, SCALE) (VALUE * SCALE)

// Control factors //

#define CTRL_SPEED_THR 10

// Rod positions //

#define  GL_ROD_Y 81.5 // Position of the goalkeeper rod
#define ATT_ROD_Y 232   // Position of the attack rod

// MM Constants //

#define MOVE_THR 10

#define MIN_GOAL_X_MM MIN_GOAL_X_CV * SCALE_X
#define MAX_GOAL_X_MM MAX_GOAL_X_CV * SCALE_X

#define MIN_ATT_X_MM MIN_ATT_X_CV * SCALE_X
#define MAX_ATT_X_MM MAX_ATT_X_CV * SCALE_X

#define MID_ATT_LO_MM MID_ATT_LO_CV * SCALE_X
#define MID_ATT_HI_MM MID_ATT_HI_CV * SCALE_X

#define MIN_GOAL_Y_MM MIN_GOAL_Y_CV * SCALE_Y
#define MAX_GOAL_Y_MM MAX_GOAL_Y_CV * SCALE_Y

#define MIN_ATT_Y_MM MIN_ATT_Y_CV * SCALE_Y
#define MAX_ATT_Y_MM MAX_ATT_Y_CV * SCALE_Y

#define MAX_ATT1_X_MM MAX_ATT1_X_CV * SCALE_X

#define MIN_ATT2_X_MM MIN_ATT2_X_CV * SCALE_X
#define MAX_ATT2_X_MM MAX_ATT2_X_CV * SCALE_X

#define MIN_ATT3_X_MM MIN_ATT3_X_CV * SCALE_X

#define MAX_HIT_RANGE_MM 10

// Misc //

#define SPEED_THR 25

#define         GL_OFF 20
#define CROSS_FIRE_OFF 15

/**********************************************************
 * Define your interpreter-compatible commands as strings *
 **********************************************************/

// Move to an extreme and reset rotation
#define BEGIN()          "BEGIN 100"
// Move towards motor by +v
#define MOVE1(pos)      ("MOVE1 " + String((int)pos))
#define MOVE2(pos)      ("MOVE2 " + String((int)pos))
// Rotate by angle
#define ROTATE1(angle)  ("ROTATE1 " + String((int)angle))
#define ROTATE2(angle)  ("ROTATE2 " + String((int)angle))
// Reset Position
//#define INITIALX()       "INITIX"


/*
 * CV Input.
 *
 * @param x         x component of ball position (width ): CV
 * @param y         y component of ball position (height): CV
 * @param timestamp Attributed timestamp to the frame
 */
typedef struct {
  int x;
  int y;
  int timestamp;
} FrameData;

FrameData currentFrame  = {-1, -1, -1};
FrameData previousFrame = {-1, -1, -1};

bool firstFrameReceived  = false;
bool secondFrameReceived = false;

/*
 * Internal information on the ball.
 *
 * @param x         x-coordinate of ball position: MM
 * @param y         y-coordinate of ball position: MM
 * @param timestamp Metrics to determine when the frame has arrived
 * @param a         Slope of the line
 * @param b         Intercept of the line
 * @param speed     Calculated speed
 */
typedef struct {
    int x;
    int y;
    int timestamp;
    int a;
    int b;
    int speed;
} Info;

Info ballData;
ParallelInterpreter interpret(
        6, 3,  7,  4, 13, 12, 5,
        2, 8, 10, 11, A3, A0, FIELD_SIZE
);

// TODO: Remove
//Movement commands for players
//double motorMovement[4]; // 0: Goalkeeper X,
//                      // 1: Goalkeeper angle,
//                      // 2: Attack rod X,
//                      // 3: Attack rod angle
/*
 * Player positions: MM
 *   [0: gl, 1: att1, 2: att2, 3: att3][x, angle]
 */
double playerPosition[4][2];

double pos_yz[2];

/*
 * Scales by the given factor to get millimeters from CV input.
 *
 * @param value Value to be scaled
 * @param scale Scaling to be applied, should be either `SCALE_X` or `SCALE_Y`
 */
// double CVtoMM(int value, double scale){
//   return value * scale;
// }

/*
 * Updates the position of the attack players.
 *
 * @param dist Distance that has been covered by the players
 */
void updateAttackPlayerX(double dist){
  for (int i = 1; i < 4; i++){
    playerPosition[i][0] += dist;
  }
}


/*
 * Retrieve ball data from CV.
 *
 * @returns frame received by CV.
 */
bool getBallData(){

    if (Serial.available() > 0) {
      // Flush incoming serial
      Serial.end();
      Serial.begin(9600);

      Serial.readStringUntil(':');
      int x = Serial.readStringUntil(';').toInt();
      int y = Serial.readStringUntil(';').toInt();

      // Check for valid x and y
      if (x <= 0 || x > CAM_WIDTH) {
          Serial.println("Invalid data received. Ignoring frame.");
          return false; // Exit early and return false
      }

      previousFrame  = currentFrame;
      currentFrame.x = x;
      currentFrame.y = y;

      if (!firstFrameReceived) {
        firstFrameReceived = true;
      }
    }
    return firstFrameReceived;
}

/*
 * Returns the closest player to the ball according to given x.
 *
 * @param plyr1 First player to compare
 * @param plyr2 Second player to compare
 * @param x     x-coordinate of ball position
 *
 * @returns the closest player to ball.
 */
int defendingAttPlayer(int p1, int p2, double x)
{
  return
    abs(playerPosition[p1][0] - x) < abs(playerPosition[p2][0] - x) ? p1 : p2;
}

/*
 * Tracks the ball with the players.
 */
void moveField(){

  double target = ballData.x;


  // Attack players position //

  double distAtt = 0;
  if (target < MIN_ATT_X_MM) {
    // Serial.println("Moving attack to minAtt");
    distAtt = MIN_ATT_X_MM - playerPosition[1][0];

  } else if (MAX_ATT_X_MM < target) {
    // Serial.println("Moving attack to maxAtt");
    distAtt = MAX_ATT_X_MM - playerPosition[3][0];

  } else if (MIN_ATT_X_MM < target && target < MIN_ATT2_X_MM){
    distAtt = target - playerPosition[1][0];

  } else if (MIN_ATT2_X_MM < target && target < MAX_ATT1_X_MM){
    distAtt = target - playerPosition[defendingAttPlayer(1,2, target)][0];

  } else if (MAX_ATT1_X_MM < target && target < MIN_ATT3_X_MM){
    distAtt = target - playerPosition[2][0];

  } else if (MIN_ATT3_X_MM < target && target  < MAX_ATT2_X_MM){
    distAtt = target - playerPosition[defendingAttPlayer(2,3, target)][0];

  } else {
    distAtt = target - playerPosition[3][0];
  }


  // Goalie position //

  double distGl = 0;
  double glPos  = playerPosition[0][0];

  if (MIN_GOAL_X_MM < target && target < MAX_GOAL_X_MM) {
    // Serial.println("Moving goalie to ball");
    distGl = target - glPos;

  } else if (target < MIN_GOAL_X_MM) {
    // Serial.println("Moving goalie to minGoal");
    distGl = MIN_GOAL_X_MM - glPos;

  } else {
    // Serial.println("Moving goalie to maxGoal");
    distGl = MAX_GOAL_X_MM - glPos;
  }


  // Move //

  if (abs(distAtt) >= MOVE_THR) {

    interpret.executeInterpreter(
      MOVE2(distAtt * FIELD_X_TO_MU)
    );

    updateAttackPlayerX(distAtt);
  }

  if  (abs(distGl) >= MOVE_THR) {

    interpret.executeInterpreter(
      MOVE1(distGl * FIELD_X_TO_MU)
    );

    playerPosition[0][0] += distGl;
  }
}

//helper function
int getClosestPlayer(){

  // Calulate the euclidian distance for the goalkeeper
  double distance = sqrt(pow(playerPosition[0][0] - ballData.x, 2) +
                         pow(GL_ROD_Y- ballData.y, 2));
  double minDistance = distance;
  double closestIndex = 0;

  //Calulate the euclidian distance to the ball for each player
  for(int i = 1; i < 4; i++) {

    // Calculate the Euclidean distance to the ball
    double distance = sqrt(pow(playerPosition[i][0] - ballData.x, 2) + pow(ATT_ROD_Y - ballData.y, 2));

    // Update the closest player if this distance is smaller
    if (distance < minDistance) {
      minDistance = distance;
      closestIndex = i;
    }
  }

  return closestIndex;

}

/*
 * Checks if shoot available and shoots the ball according to the given
 * range if it is.
 *
 * @param rangeLo The smallest accessible location to the player
 * @param rangeHi The largest accessible location to the player
 */
void checkAndShoot()
{

  // Check player that attacks and add treshold
  int index = getClosestPlayer();

  if(index == 0) {
    int x_min = playerPosition[0][0] - MAX_HIT_RANGE_MM;
    int x_max = playerPosition[0][0] + MAX_HIT_RANGE_MM;

    if (MIN_GOAL_Y_MM < ballData.y && ballData.y < MAX_GOAL_Y_MM
    &&  x_min < ballData.x && ballData.x < x_max) {
    Serial.println("Shooting with Goalie !");
    interpret.executeInterpreter(
      ROTATE1(-200)
    );
    }
  }

  if (MIN_GOAL_Y_MM < ballData.y &&
      ballData.y < MAX_GOAL_Y_MM) {
    Serial.println("Shooting with Goalie!");
    interpret.executeInterpreter(
      ROTATE1(-200)
    );
  }

  if (MIN_ATT_Y_MM < ballData.y &&
      ballData.y < MAX_ATT_Y_MM) {
    Serial.println("Shooting with Attacker!");
    interpret.executeInterpreter(
      ROTATE2(-200)
    );
  }

  delay(500);
}


void setup() {

  Serial.begin(9600);
  playerPosition[0][0] = CV_TO_MM(PLAYER_0_X, SCALE_X);
  playerPosition[1][0] = CV_TO_MM(PLAYER_1_X, SCALE_X);
  playerPosition[2][0] = CV_TO_MM(PLAYER_2_X, SCALE_X);
  playerPosition[3][0] = CV_TO_MM(PLAYER_3_X, SCALE_X);

  interpret.setupSteppers();
  delay(1000);
  interpret.executeInterpreter(BEGIN());

}

void loop() {

  if (!getBallData()){
     return;
  }

  //Serial.println(currentFrame.y);


  ballData.x = CV_TO_MM(currentFrame.x, SCALE_X);
  ballData.y = CV_TO_MM(currentFrame.y, SCALE_Y);

  //Serial.println(currentFrame.y);

  moveField();
  checkAndShoot();


  interpret.moveMotorsWithSensors();
  /*while (interpret.stepperX.distanceToGo() != 0 ||
         interpret.stepperY.distanceToGo() != 0 ||
         interpret.stepperZ.distanceToGo() != 0 ||
         interpret.stepperA.distanceToGo()) {
    interpret.stepperX.run();
    interpret.stepperY.run();
    interpret.stepperA.run();
    interpret.stepperZ.run();
  }*/
}

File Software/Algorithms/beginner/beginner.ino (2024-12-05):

#include <stdio.h>
#include <math.h>


//constants
#define controlSpeedThreshold 10
#define controlPositionThresholdX 15
#define controlPositionThresholdY 15
#define rod0_Y 81.5                   //position of the goalkeeper rod
#define rod1_Y 232                    //position of the attack rod
#define speedThreshold 25
#define fieldWidth   680
#define fieldHeight  605
#define cameraWidth  640
#define cameraHeight 480 
#define offsetGoalie 20 
#define crossFireOffset 15
#define minGoal 250
#define maxGoal 430
#define motorUnits 350
#define physicalRangeMM 70

double scaleX = fieldWidth/ cameraWidth;    //ratio of cv coordinates into the field dimension
double scaleY = fieldHeight/ cameraHeight;
double motorScalingFactor = motorUnits / physicalRangeMM ;

//inputs of the cv
typedef struct {
  double x;
  double y;
  double timestamp;
} FrameData;

FrameData currentFrame = {-1,-1,-1};
FrameData previousFrame = {-1,-1,-1};

bool firstFrameReceived = false;
bool secondFrameReceived = false;

typedef struct {
    double x;          // x-coordinate of posB
    double y;          // y-coordinate of posB
    double timestamp;  // when the frame arrived
    double a;          // Slope of the line
    double b;          // Intercept of the line
    double speed;      // Calculated speed
} Infos;

Infos ballData;

//Movement commands for players
double motorMovement[4]; // 0: Goalkeeper X, 1: Goalkeeper angle, 2: Attack rod X, 3: Attack rod angle
double playerPosition[4][2]; // Player positions: [x, angle]

//retrieve ball data
bool getBallData(){

  //process all lines in the buffer
  while (Serial.available() > 0){

    //String fromatted as ":x;y;timestamp"
    String data = Serial.readStringUntil('\n');
    double newX, newY, newTimestamp;
    if(sscanf(data.c_str(), ":%lf;%lf;%lf", &newX, &newY, &newTimestamp) == 3){

      Serial.print(newX);
      Serial.print(newY);
      Serial.print(newTimestamp);
      //update frame data
      previousFrame = currentFrame;
      currentFrame.x = newX * scaleX;  //map camera coordinates to field coordinates
      currentFrame.y = newY * scaleY;
      currentFrame.timestamp = newTimestamp;

      // Update frame reception
      if (!firstFrameReceived) {
        firstFrameReceived = true; // The first frame has been received
      }
    }
  }

  ballData.x = currentFrame.x;
  ballData.y = currentFrame.y;
  ballData.timestamp = currentFrame.timestamp;

  return firstFrameReceived;

}

//get ball.a, ball.b, ball.speed
void calculateBallTrajectory(){

  static double previousX = 0;
  static double previousY = 0;
  static double previousTime = 0; //ms

  if (currentFrame.timestamp > -1){
    double deltaTime = ballData.timestamp - previousTime;

    if (deltaTime > 0){

      //complete linear equation ax + b
      if(ballData.x != previousX){
        ballData.a = (ballData.y - previousY) / (ballData.x - previousX); // a = y2-y1/ x2-x1
        ballData.b = ballData.y - ballData.a * ballData.x; // b = y2 - a * x2
      }
      else{
        ballData.a = 0;
        ballData.b = ballData.x; //Vertical line stays at x position
      }

    //calculate speed
    ballData.speed = sqrt(pow((ballData.x - previousX), 2) + pow((ballData.y - previousY), 2)) / deltaTime; // v = d/t
    }
  }
  else{
    ballData.a = 0; //first time function is called
    ballData.b = currentFrame.y;
    ballData.speed = 0;
  }

  //update variables
  previousX = ballData.x;
  previousY = ballData.y;
  previousTime = ballData.timestamp;

}

//helper function
int getClosestAttackPlayerIndex(double x, double y){

  int closestIndex = -1;
  double minDistance = 1e5;

  //Calulate the euclidian distance to the ball for each player
  for (int i = 1; i < 4; i++) { //only attack players (index 1, 2, 3)
    double playerX = playerPosition[i][0];
    double playerY = rod1_Y;

    // Calculate the Euclidean distance to the ball
    double distance = sqrt(pow((x - playerX), 2) + pow((y - playerY), 2));

     // Update the closest player if this distance is smaller
    if (distance < minDistance) {
      minDistance = distance;
      closestIndex = i;
    }
  }

  return closestIndex;

}

bool isBallControlled(){

  int closestAttackerToBall = getClosestAttackPlayerIndex(ballData.x, ballData.y);

  //check if ball is controlled by the goalkeeper
  bool isNearRod0 = (abs(ballData.x - playerPosition[0][0]) <= controlPositionThresholdX) &&
                      (abs(ballData.y - rod0_Y) <= controlPositionThresholdY);

  //check if ball is controlled by a player of the attack rod
  bool isNearRod1 = (abs(ballData.x - playerPosition[closestAttackerToBall][0]) <= controlPositionThresholdX) &&
                      (abs(ballData.y - rod1_Y) <= controlPositionThresholdY);

  //check that the ball is slow enough
  bool isSpeedLow = ballData.speed <= controlSpeedThreshold;

  return (isNearRod0 || isNearRod1) && isSpeedLow;

}

//helper function
void rotateAndUpdatePlayers(double y){
  motorMovement[3] = y;
  ROTATE(y);
  for (int i = 1; i < 4; i++){
      playerPosition[i][1] = y;
  }
}

//helper function
void translateAndUpdatePlayers(double x){
  motorMovement[2] = x * motorScalingFactor;
  MOVE(motorMovement[2]);
  for (int i = 1; i < 4; i++){
      playerPosition[i][0] += x;
  }
}

void takeDefensePosition(){

  //find player closest to new pos of the ball and calculate the distance
  double predictedX = (rod1_Y - ballData.b)/ ballData.a;
  double defenderIndex = getClosestPlayerIndexAttack(predictedX, rod1_Y);
  double defenderX = playerPosition[defenderIndex][0];
  int rodTranslation = predictedX - defenderX;

  //rotate player accordingly to defense positions
  if (abs(ballData.speed) <= speedThreshold){
    ballData.speed >= 0 ? rotateAndUpdatePlayers(-30) : rotateAndUpdatePlayers(30);
  }
  else{
    rotateAndUpdatePlayers(-30);
  }

  //move rod to intercept ball
  translateAndUpdatePlayers(rodTranslation);

  //offset gardian depending on the half of the field the ball comes from
  if(ballData.x <= fieldWidth/2){
    motorMovement[0] = rodTranslation - offsetGoalie;  //offset the goalkeeper to the left of the attacker
    MOVE(motorMovement[0])
    playerPosition[0][0] += rodTranslation - offsetGoalie;
  }else{
    motorMovement[0] = (rodTranslation + offsetGoalie) * motorScalingFactor;
    MOVE(motorMovement[0])                            //offset the goalkeeper to the right of the attacker
    playerPosition[0][0] += rodTranslation + offsetGoalie;
  }

}

//helper function
void alignMiddlePlayerWithGoalkeeper(){

  double alignement = playerPosition[0][0] - playerPosition[2][0];
  double receivePass = 30;

  translateAndUpdatePlayers(alignement);
  rotateAndUpdatePlayers(receivePass);

}

//helper function
void passBallToMiddlePlayer(){

  while(rod0_Y + controlPositionThresholdY / 2){
    motorMovement[1] -= 5;
    ROTATE(-5);
    playerPosition[0][1] -5= ;
  }

}

//helper function
void hitBallFront(){

  motorMovement[3] = -360;
  ROTATE(-360);
  INITALY;

}
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

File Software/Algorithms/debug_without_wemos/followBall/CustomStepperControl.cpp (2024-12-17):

#include "CustomStepperControl.h"

// Constructor
CustomStepperControl::CustomStepperControl(int yDir, int yStep, int xDir, int xStep, int enPin, int sensor1Y, int sensor2Y, int sensor1X, int sensor2X)
  : stepperY(1, yStep, yDir),
    stepperX(1, xStep, xDir)
{
  Y_DIR = yDir;
  Y_STP = yStep;
  X_DIR = xDir;
  X_STP = xStep;
  EN = enPin;
  this->sensor1Y = sensor1Y;
  this->sensor2Y = sensor2Y;
  this->sensor1X = sensor1X;
  this->sensor2X = sensor2X;
}

void CustomStepperControl::setBeginning() {
  Serial.println("setBeginning() called.");
  int big_distance = 2000; //max distance in motorstep for translation
  moveSide(stepperY, sensor1Y, sensor2Y, big_distance);
  moveSide(stepperX, sensor1X, sensor2X, big_distance);
  stepperY.setCurrentPosition(0);
  stepperX.setCurrentPosition(0);
  Serial.println(stepperY.currentPosition());
  Serial.println(stepperX.currentPosition());
  moveSide(stepperY, sensor1Y, sensor2Y, -big_distance);
  moveSide(stepperX, sensor1X, sensor2X, -big_distance);
  int max_translation = stepperY.currentPosition();
  moveSide(stepperY, sensor1Y, sensor2Y, -max_translation/2 * 5);
  moveSide(stepperX, sensor1X, sensor2X, -max_translation/2 * 5);
  // Move into -z direction


  //   // for both stops when the sensor is triggered
  // int middlePosition = -(40/2 * 5)/2 ;  //translation_width/2 * fieldXToMotorUnits

  // rotateByAngle(wemosSerial1, 0);
  // rotateByAngle(wemosSerial2, 0);

  // moveSide(stepperY,sensor1Y, sensor2Y, middlePosition);
  // stepperY.setCurrentPosition(middlePosition); // now this is 0 position

  // moveSide(stepperX,sensor1X, sensor2X,middlePosition);
  // stepperX.setCurrentPosition(middlePosition); // now this is 0 position
}

// MOVE <value>
// <0 values to go far from the side motor
// >0 values to come close to the side motor
// for 7cm mov range of player, 350 unit is good
// original 22 cm
void CustomStepperControl::moveSide(AccelStepper &stepper, int sensor1, int sensor2, int value) {
  //int y =  stepper.currentPosition();
  stepper.move(value);          // Set the final position
  //for coordinate value thats been going far from the side motor >0, controlled by the pin 11
  if(value>0){
    while (digitalRead(sensor1) == LOW && digitalRead(sensor2) == LOW && stepper.distanceToGo() != 0) {
      Serial.println(digitalRead(sensor1));
      Serial.println(digitalRead(sensor2));
      stepper.run();                  // Continuously move toward the target
    }
    stepper.stop();
    stepper.runSpeedToPosition();
  }
  else {
    while (digitalRead(sensor1) == LOW && digitalRead(sensor2) == LOW && stepper.distanceToGo() != 0) {
      Serial.println(digitalRead(sensor1));
      Serial.println(digitalRead(sensor2));
      stepper.run();                  // Continuously move toward the target
    }
    stepper.stop();
    stepper.runSpeedToPosition();
  }
  Serial.print("Moved by ");
  Serial.println(value);
}


void CustomStepperControl::returnToInitialPositionSide() {
  stepperY.moveTo(0);
  stepperX.moveTo(0);
  stepperY.runToPosition();
  stepperX.runToPosition();
}

// void CustomStepperControl::rotateByAngle(SoftwareSerial &serialPort, float angle) {
//   float rad_angle = angle * 3.14 / 180;
//   String command = "MOVE " + String(rad_angle);
//   serialPort.println(command);
// }

void CustomStepperControl::executeInterpreter(String command) {
  char cmd[20];
  int value;
  sscanf(command.c_str(), "%s %d", cmd, &value);

  if (strcmp(cmd, "MOVE1") == 0) {
    moveSide(stepperY, sensor1Y, sensor2Y, value);
  } else if (strcmp(cmd, "MOVE2") == 0) {
    moveSide(stepperX, sensor1X, sensor2X, value);
  // } else if (strcmp(cmd, "ROTATE1") == 0) {
  //   rotateByAngle(wemosSerial1, (float)value);
  // } else if (strcmp(cmd, "ROTATE2") == 0) {
  //   rotateByAngle(wemosSerial2, (float)value);
  } else if (strcmp(cmd, "INITIALX") == 0) {
    returnToInitialPositionSide();
  } else if (strcmp(cmd, "BEGIN") == 0) {
    setBeginning();
  } else {
    Serial.println("Invalid Command!");
  }
}

void CustomStepperControl::setupSteppers() {
  Serial.begin(9600);

  stepperY.setMaxSpeed(500.0);
  stepperY.setAcceleration(4000.0);
  stepperX.setMaxSpeed(500.0);
  stepperX.setAcceleration(4000.0);

  pinMode(EN, OUTPUT);
  digitalWrite(EN, LOW);

  // pinMode(sensor1Y, INPUT);
  // pinMode(sensor2Y, INPUT);
  // pinMode(sensor1X, INPUT);
  // pinMode(sensor2X, INPUT);
}

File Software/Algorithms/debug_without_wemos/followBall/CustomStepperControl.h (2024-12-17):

#ifndef CUSTOM_STEPPER_CONTROL_H
#define CUSTOM_STEPPER_CONTROL_H

#include <AccelStepper.h>
#include <Arduino.h>

class CustomStepperControl {
  public:
    CustomStepperControl(int yDir, int yStep, int xDir, int xStep, int enPin, int sensor1Y, int sensor2Y, int sensor1X, int sensor2X);

    void setBeginning();
    void moveSide(AccelStepper &stepper, int sensor1, int sensor2, int value);
    void returnToInitialPositionSide();
    //void rotateByAngle(SoftwareSerial &serialPort, float angle);
    void executeInterpreter(String command);
    void setupSteppers();

  private:
    // Goalee
    AccelStepper stepperY;
    // Attack
    AccelStepper stepperX;
    int EN;
    int Y_DIR, Y_STP, X_DIR, X_STP;
    int sensor1Y, sensor2Y, sensor1X, sensor2X;
    const float stepsPerMM = 400.0;
    const float stepsPerRevolution = 3200.0;
    const float degreesPerStep = 360.0 / stepsPerRevolution;
    int acceleration = 5;
};

#endif // CUSTOM_STEPPER_CONTROL_H

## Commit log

2024-11-07 Upload Documents
    Add current versions of :
    - Project Proposal
    - Electronics Chart
    - Bill of Materials
2024-11-08 Code for Camera Blinking (#21)
2024-11-08 Add code for camera webserver example (#21) Note: Couldn't connect to my hotspot
    [partitions.csv]
2024-11-11 Added CameraWebServer example code
    [partitions.csv]
2024-11-11 Cleaning up
    [partitions.csv]
2024-11-12 Updating the arduino program (#21)
2024-11-13 Removed Encoding in Base64 (#21) Removing encoding seems to solve issues we are having. We still need to chek on the computer whether it is indeed an image
    [transmit-single-img-over-serial.ino]
2024-11-14 Fixed a few errors in the implementation
    Note: We do get an image that should be valid according to `jpeg`
    standards (starting with <ff><d8><ff> and ending with <ff><d9>) but the
    image is not understood by an image viewer
    [main.py]
2024-11-15 Add files via upload
    isolation code for the side to side motion
    arduino cnc shield, Y axis , nemo 17 motor with A4988 motor driver
2024-11-17 Switched from `BmpArray` class inheriting from `numpy.ndarray` to storing one (#21)
    It turns out that inheriting the `numpy.ndarray` does not seem to work
    or involves too much manipulation to be convenient
    [main.py]
2024-11-18 Add files via upload
    Optical Switch End Stop sensor check if it responds to action ,Arduino blinks if a paper interacts, bumps into the sensor
2024-11-19 Switch from Bitmap to matplotlib (#21) Uses matplotlib to store the image instead of Bitmap. Problems with headers and bytes are no longer a concern when using matplotlib.
2024-11-20 Added transmit image through hotspot (#21)
    [partitions.csv]
2024-11-22 Add Interpreter, Documentation, Small Fixes (#21) - Adds a command line interpreter that accepts different arguments for easier and quicker debugging (e.g. if no output serial port is connected) - Ad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
    [main.py]
2024-11-22 Small Fix of CLI input
    [main.py]
2024-11-22 Fixing reception of images from url and Debugging (#21)
    [main.py]
2024-11-26 Create init.txt
    Add folder for CAD to put in the stl and dxf files
2024-11-26 Create PoleComponents
    Create specialised folders for different parts of the CAD
2024-11-27 Over webcam works (#21)
    [partitions.csv]
2024-11-27 Adding QR marker detection & Rework the Interpreter (#21) - Rework the possible command line flags and their usage - Add code for detecting QR Markers and transforming the image prior to processing i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
    [main.py]
2024-11-27 isolation test for rotary motor
    code taken from code/actuators/SimpleFOC/stepper_L298N/WEMOS_D1_R32/stepper_L298N_D1.ino in resourses
2024-11-27 Add QR Markers for Printing (#64)
2024-11-27 Fix QR Marker Detection & Image Transformation (#64, #39) - Fix QR Marker Detection - Fix Image transformation - Change Radius to work with transformed image - Improve debugging capabilities
    [main.py]
2024-11-29 Extend Cmd Line Interpreter (#64) - Add Flag to define a window scale since the windows are normally too big for the screen - Change Flag -useQR to -noQR and its usage. The reason for that is that th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
    [main.py]
2024-11-29 Added some directories to archive
    [partitions.csv]
2024-12-02 Create arduino_control_motors.ino
    integration code for rotary and sideway motors, controlled by central arduino
2024-12-02 Create wemos_integratino_arduino.ino
    receiver wemos code , receives commands from arduino uno
2024-12-02 need a beginner folder for arduino uno ide
2024-12-03 added correct define values + added the conversion of camera dimension to field dimension
    [beginner.ino]
2024-12-04 fix compilation error + add scaling factor for motor movement
    [beginner.ino]
2024-12-04 Establish communication between laptop and Arduino
2024-12-04 Add Program that detects button press (#69) Add Program that detects when the reset button is pressed and sets an output pin to high for a specified amount of time.
2024-12-05 cameraHeight value correction
2024-12-06 Add incomplete skecth for testing Motor Control (#65) - Add Sketch scaffholding - Add Constants for conversion between coordinates of game logic and interpreter - Add Test cases for rotation (current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
2024-12-06 Improve Sketch for testing Motor Control (#65) - Update Values for max Motor Units and corresponding distance in mm - Include motor id in interpreter calls. So one can now decide which motor to contr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
2024-12-09 Switch timestamp to arduino code
2024-12-09 Fix noQR and windows Flag (#74)
    [main.py]
2024-12-09 Implement Solution to Ball distortion by transformation (#74) - Add mode to detect one QR Marker and store its last position (the origin of the field) - Add Flag -c or --cameraOrigin to remove this b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
    [main.py]
2024-12-10 Fix CLI throwing error without -w flag (#74)
    [main.py]
2024-12-13 Fix Image Transformation (#74) - Move definition of destination points into the loop and make them depend on the distances between the QR Markers - Fix instantiation of last known marker positions - 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
    [main.py]
2024-12-13 Improve Documentation, Code Cleanup and CLI (#74) - Add flag -l or --clr-det to activate color Detection (to reduce detected circles) - Add Flag -p or --port to define a serial port for the output - 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
2024-12-16 Fixed the port input
    [main.py]
2024-12-16 Add documentation to Arduino algorithm
2024-12-16 Fill List of Materials (#82)
2024-12-17 Write Sections Project Structure & Uploading code to the Arduino (#82)
2024-12-17 Add the beginning of the game by setting up motor positions
2024-12-17 Fix the port input
    [main.py]
2024-12-17 Update README.md
    - Change H-Bridge to CNC shield in List of materials
    - Moved section of Computer vision to the end
    - Updated the instructions for setting up the computer vision
2024-12-18 Add millimiter as a main metric and difference in ball position threshold for the player to move
2024-12-18 Change motor speed and implement some heuristics
2024-12-19 Reorganise repository and add radii flag for camera vision
    [partitions.csv]
2024-12-19 All the DXF files to laser-cut
    [BlockerPulleyHolder.dxf, Bottom.dxf, ExternBoardMotorSide.dxf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]
2024-12-19 Mechanical component that should be 3D printed
    [AdptaterNemaToPole.stl, AluminiumHolders.stl, BigPlasticPulley.stl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]
2024-12-19 submitted clean version of CAD for pole components and electronics
    [10uFCap.f3d, 17HS4401S Stepper Motor.f3d, A4988-Stepper-Driver-WithPins.f3d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]
2024-12-19 Put steppers as private attributes
2024-12-20 Update Path to arduino code in README
2024-12-22 Just changed the right path to Arduino code + code from demo Friday
